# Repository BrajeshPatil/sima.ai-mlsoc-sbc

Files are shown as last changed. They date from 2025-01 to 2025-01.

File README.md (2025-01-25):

# sima.ai_mlsoc_sbc
The Single Board Computer designed using the SiMa.ai MLSoC is a part of a project that I did under ARTPARK. The SBC was designed to run computationally heavy software such as SLAM, VIO, and Autonomous Guidance Systems for UAV applications. The SiMa.ai MLSoC, a state-of-the-art ML-based SOC, was selected for this purpose.

This repository provides the design files for only the hardware part of the project. [Altium Designer](https://www.altium.com/altium-designer) has been used for designing the Single Board Computer.

# Hardware Architecture
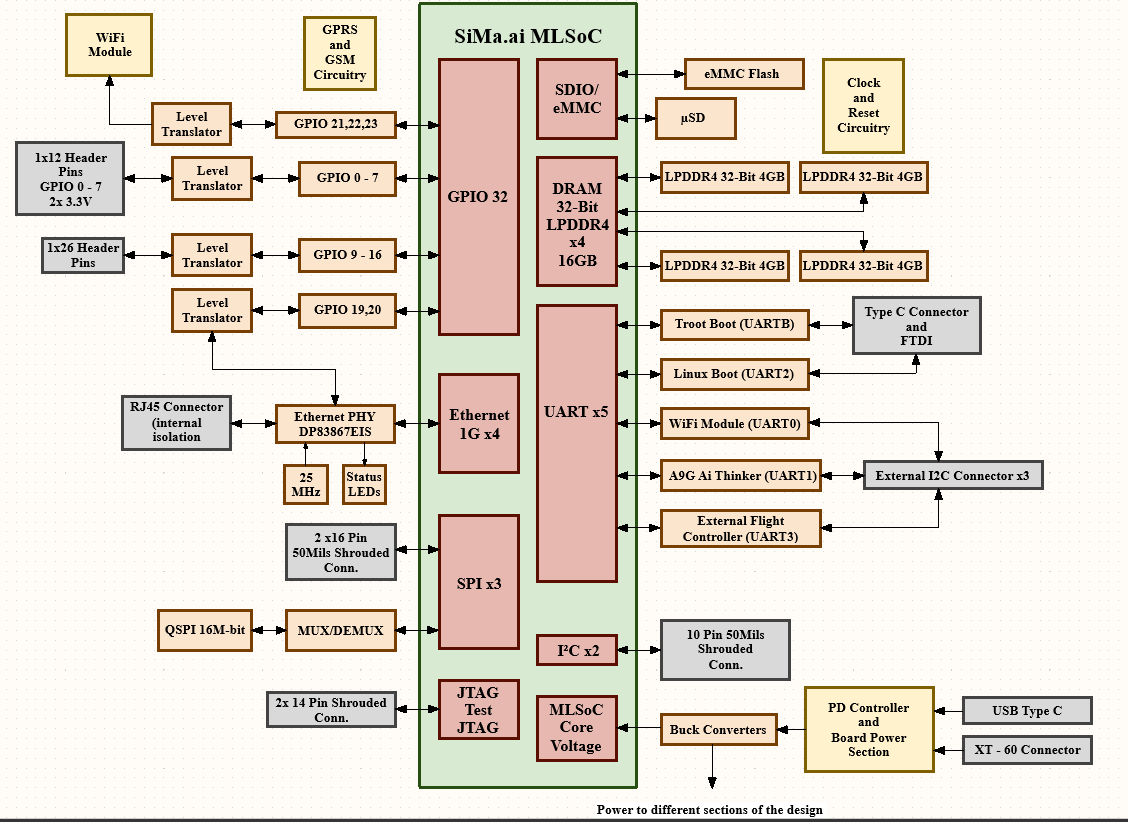
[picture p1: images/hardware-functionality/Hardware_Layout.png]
Hardware Layout


Features of the SBC:
1. SiMa.ai MLSoC provides 4 Ethernet Chipsets. Only 1 of these chipsets have been used in our SBC. The Ethernet PHY IC DP83867EIS has been used for implementing the physical layer for Communication. RJ45 Connectors with internal magnetic isolation have been used.
2. 5 UART Controllers have been used for working of the following sub-systems:
    - UART0 Controller has been used for functioning of the WiFi Module.
    - UART1 Controller has been used for functioning of A9G AI Thinker GSM and GPRS module.
    - Linux Boot functionality is provided by using UART2 and Troot Boot has been implemented using UARTB. These are also connected to FTDI chip so that the SBC can be booted using a Type C Cable.
    - UART3 currently doesn't have any functionality but has been made accessible. It can be used to communicate with an external UART device.
    - UART0, UART1 and UART3 have been connected to external I2C connectors.  
3. The SoC contains 32 GPIO pins. They are implemented as follows:
    - GPIO Pins 21, 22 and 23 have been used in the WiFi Module. As the WiFi Module works on 3.3V voltage level, a (1.8V to 3.3V) voltage translator has been used.
    - GPIO Pins 0 - 7 have been translated to 3.3V and have been provided externally.
    - GPIO Pins 9 - 16 have been translated to 5V and have been provided externally.
    - GPIO Pins 19, 20 have been used for functioning of the Ethernet PHY IC.
4.  DRAM (Dynamic Random-Access Memory) is fast, temporary storage that holds data while a computer runs, but it loses information when powered off. It stores data in capacitors that require periodic refreshing, using operations like activate, read/write, precharge, and refresh to manage access and integrity. 4x 32-bit LPDDR4 chipsets with P/N MT53E1G32D2FW-046 IT:B from Micron is mounted on the MLSoC Evaluation Board. The operating frequency of the LPDDR4 chip is 1866MHz.
5. The SBC can be powered through two ways, i) USB Type C and ii) XT-60 Connector.
    - The TPS548D22 IC is used to generate 0.85V Core Voltage.
    - SiC437DED used for generating 1.8V and 1.1V.
    - The PMIC Switching Regulator is used to generate 3.3V, 1.8V, 2.5V and 4.2V.
6. The SoC contains 3 SPI Buses.
    - 1 SPI Bus has been provided externally.
    - The other 2 SPI Buses have been used to implement a QSPI Flash Memory using a MUX and a DEMUX. 
7. The 2 I2C Buses have been provided on the SBC. These can be used for interfacing with sensors, storage devices, displays or any device working on I2C Protocol.
8. The eMMC interface includes a clock (CLK), command (CMD), and an 8-bit data bus (D0-D7), with separate power pins for core (VCC), I/O (VCCQ), and stabilization (VDDI). It also features DS for HS-400 mode, card detect (CRD DET N), and write protect (CRD WR PROT) functionality.
9. The MLSoCsupports SD3.0 controller interface for loading the boot files from an external SD card. A Micro-SD Push-Push connector with P/N 693071020811 is used for interfacing the external SD card with the MLSoC Evaluation Board.
10. JTAG Test functionality has been provided by providing access to them through a 2x14 Pin Shrouded Connector.
11. The GPS and GSM functionalities for tracking the vehicle's location and enabling SMS communication have been implemented using the A9G Ai-Thinker module. The clock and reset circuitry has also been employed. 

# File structure
The repository contains directories for all sub-sections of the hardware layout. In-depth explanation of all the sub-sections have been included in these directories.
```
.
│   LICENSE                        # This file contains the license information for the project.
│   README.md                      # This file provides an overview of the project.
├───Boot Modes and Status
│   │   README.md                  # Description of boot modes and status indicators.
│   └───Altium Designer Files      # Contains Altium Designer files related to boot modes and status.
├───DRAM Interface
│   │   README.md                  # Information about DRAM interface and configurations.
│   └───Altium Designer Files      # Contains Altium Designer files related to the DRAM interface.
├───Gigabit Ethernet
│   │   README.md                  # Details about Gigabit Ethernet setup and configurations.
│   └───Altium Designer Files      # Contains Altium Designer files for Gigabit Ethernet.
├───GPIO
│   │   README.md                  # General Purpose Input/Output (GPIO) configurations and usage.
│   └───Altium Designer Files      # Contains Altium Designer files for GPIO.
├───GSM and GPS Module
│   │   README.md                  # Documentation for GSM and GPS module integration.
│   └───Altium Designer Files      # Contains Altium Designer files for GSM and GPS module.
├───I2C Bus
│   │   README.md                  # Information about the I2C Bus interface and connections.
│   └───Altium Designer Files      # Contains Altium Designer files for the I2C Bus.
├───images
│   ├───hardware-design            # Images related to hardware design.
│   └───hardware-functionality     # Images showing hardware functionality.
├───Non Volatile Memory
│   │   README.md                  # Documentation on non-volatile memory usage and types.
│   └───Altium Designer Files      # Contains Altium Designer files for non-volatile memory.
├───Power Management
│   │   README.md                  # Details about power management strategies and configurations.
│   └───Altium Designer Files      # Contains Altium Designer files for power management.
├───SPI Bus
│   │   README.md                  # Information about SPI Bus interface and protocols.
│   └───Altium Designer Files      # Contains Altium Designer files for SPI Bus.
├───System Clocks
│   │   README.md                  # Documentation on system clocks and timing configurations.
│   └───Altium Designer Files      # Contains Altium Designer files for system clocks.
├───UART
│   │   README.md                  # Information about UART (Universal Asynchronous Receiver-Transmitter) interface.
│   └───Altium Designer Files      # Contains Altium Designer files for UART interface.
└───WiFi Module
    │   README.md                  # Documentation on WiFi module setup and configurations.
    └───Altium Designer Files      # Contains Altium Designer files for WiFi module.                   
```
# Contributors
- [Karteek Nayak](https://github.com/Karteek-N)
- [Brajesh Patil](https://github.com/BrajeshPatil)

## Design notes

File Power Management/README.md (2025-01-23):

# Power Management
### Power Input and Supply

The power section of this Single Board Computer (SBC) is designed to support multiple input options for versatility and efficiency. Below are the key features of the power input design:

#### Input Connectors
XT60 Connector: A robust input option suitable for high-current applications.
USB Type-C Connector: A modern and widely used connector for both data and power delivery.

#### USB PD Protocol
The power delivery system leverages the USB Power Delivery (USB PD) protocol to achieve higher power requirements, supporting up to 20V at 5A (100W). This enables the SBC to handle high-performance applications while maintaining efficient power utilization.

### Key Components
Communication Lines: The USB PD protocol relies on the CC1 and CC2 lines for communication. These lines establish a standardized negotiation process for voltage and current levels, ensuring compatibility and safety.

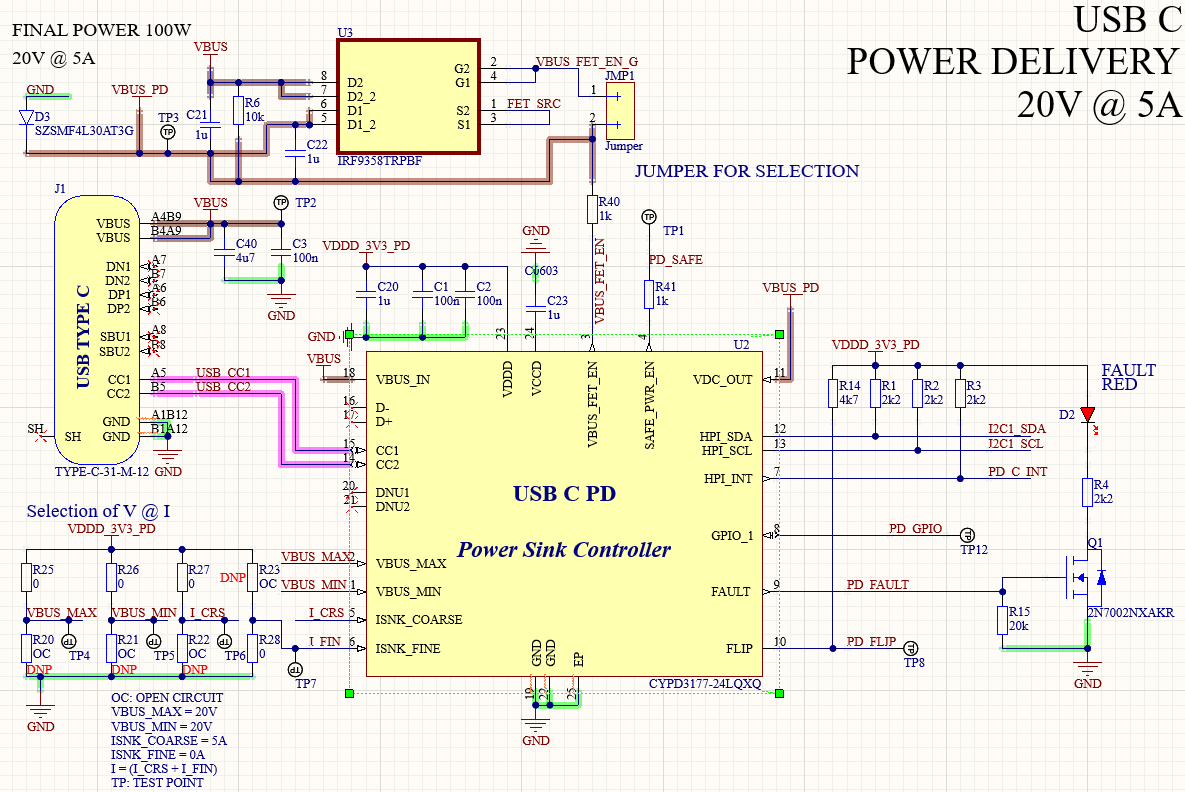
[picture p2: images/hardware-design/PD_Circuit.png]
Image description


Current Setting Lines: The CC1 and CC2 lines also play a crucial role in setting the appropriate current levels, adhering to the USB PD specifications.

PD Controller: The SBC uses the CYPD3177-24LQXQ by Infineon as the USB PD controller.

### Layout
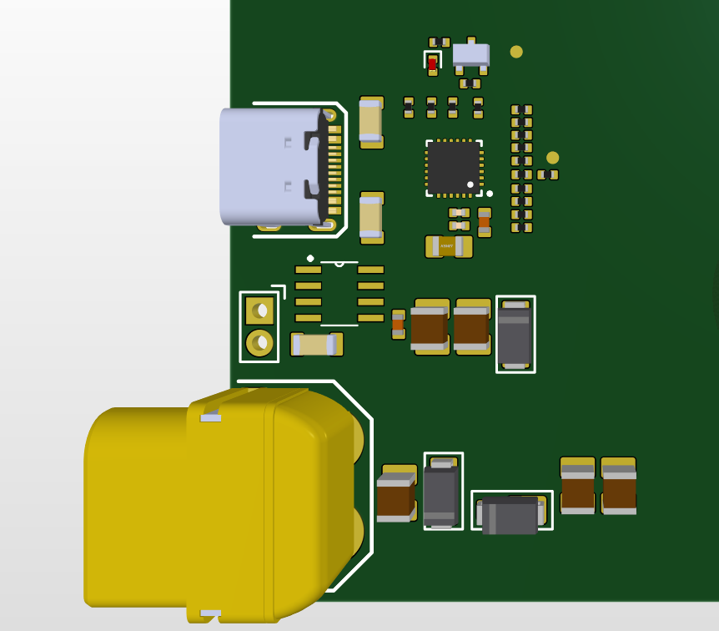
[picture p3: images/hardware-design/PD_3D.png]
Image description


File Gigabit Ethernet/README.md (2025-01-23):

# Gigabit Ethernet
This section explains the schematic design implementation of the Gigabit Ethernet using the DP83867 Ethernet PHY IC. This feature is added in our SBC so that the pilot can be able to communicate with other devices supporting Ethernet or get inbuilt access to the Internet and additional functionality can be added later as required.

### Hardware Architecture
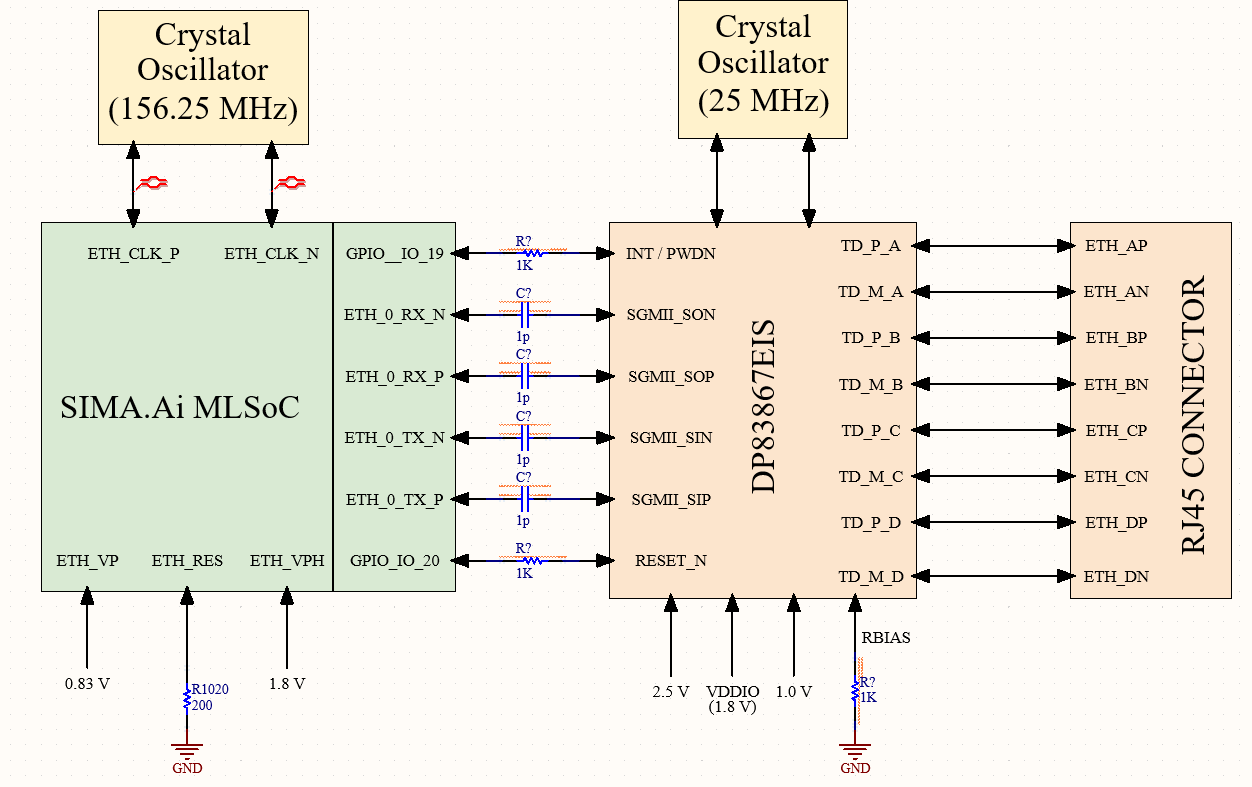
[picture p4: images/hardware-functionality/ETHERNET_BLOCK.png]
Hardware Layout


The MLSoC provides 4 chipsets of Ethernet but the SBC is provided with one Gigabit Ethernet chipset. The Ethernet MAC is interfaced with the RJ45 Magjack connector with the help of the Ethernet PHY DP83867EIS IC.
Magnetic isolation to prevent signal form back routing is also taken care of while designing. Appropriate Crystal values were used for the oscillators of the Ethernet MAC and the Ethernet PHY. 156.25 MHz Crystal was used for the internal working of the Ethernet MAC.

### Schematic
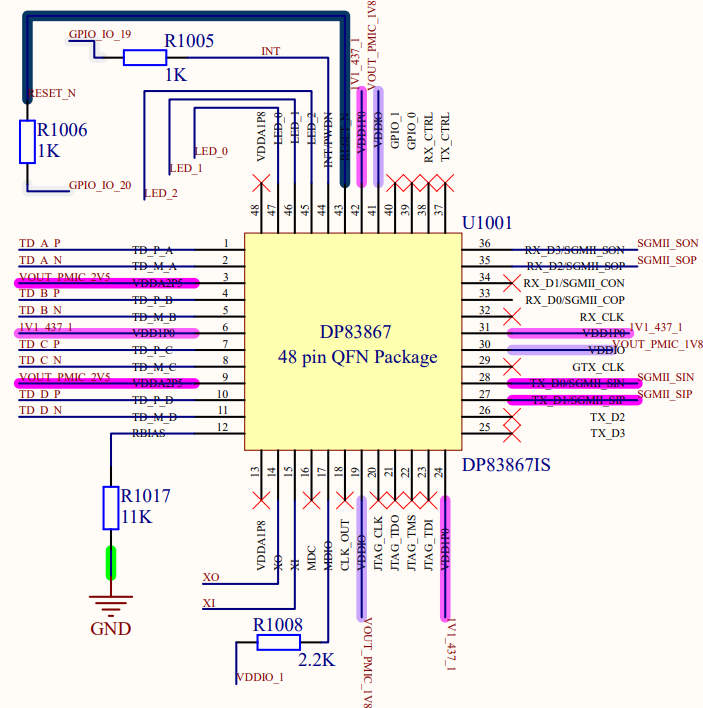
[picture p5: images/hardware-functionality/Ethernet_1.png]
Image description

We have used the 2 power supply mode of the IC. An 11kΩ bias resistor is used as per the datasheet. INT(44) and RESET N(43) are connected to MLSoC GPIOs for external user control.

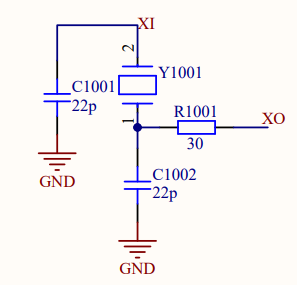
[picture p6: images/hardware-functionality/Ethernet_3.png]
Image description


The clock input is provided through a 25MHz crystal. The crystal load capacitance is calculated using ((CX1 x CX2) / (CX1 + CX2)) + Cstray. Resistance is 30 ohms and crystal load capacitance is 22pF. This crystal oscillator is connected to pins XO(14) and XI(15).

The Ethernet PHY is connected to MLSoC with the 4 pin mode. These 4 pins are SGMII_SON(36), SGMII_SOP(35), SGMII_SIN(28), SGMII_SIP(27). SGMII_SON and SGMII_SOP are used for the receiving signal and form a differential pair. They are connected to the ETH_0_RX_N and ETH_0_RX_P using a resistor divider network and 0.1µ F capacitors.

SGMII_SIN and SGMII_SIP form a differential pair and are used to transmit. Rhi = 4K and Rlo = 10K are used on pins 27,28,35,36.

The LED_0, LED_1 and LED_2 pins are used as strapping options to select particular modes.

### Power Sub-Section
Image description

It is possible to operate the DP83867 using two or three power supplies. Although the two supply configuration requires slightly more power, it requires less space as compared to its counterpart. So we have used the three power supply configuration.

VDDA1P8 pin is left unconnected. We have connected 1µF and 0.1µF decoupling capacitors as close as possible to component VDD pins and 0.1µF capacitor closest to the pin. In our SBC we have used VDDIO as 1.8 V. The power required for this IC is 495 mW.

### Boot Strapping
Image description

The DP83867 has multiple functional pins which provide strapping options which help the device work into specific modes. Values of these pins are sampled at power up or hard reset. Strap Configuration can be defined by two resistors Rhi and Rlo. Values of these resistors can be set in order to select one of the four modes. We have used SGMII ENABLE i.e. Mode 1 for LED_0.

### Ideal Resistor Values for Strapping Configurations
| Mode | Vmin (V) | Vtyp (V) | Vmax (V) | Ideal Rhi (kΩ) | Ideal Rlo (kΩ) |
|---|---|---|---|---|---|
| 1 | 0 | 0 | 0.098 * VDDIO | OPEN | OPEN |
| 2 | 0.140 * VDDIO | 0.165 * VDDIO | 0.191 * VDDIO | 10 | 2.49 |
| 3 | 0.225 * VDDIO | 0.255 * VDDIO | 0.284 * VDDIO | 5.76 | 2.49 |
| 4 | 0.694 * VDDIO | 0.783 * VDDIO | 0.888 * VDDIO | 2.49 | OPEN |

### Modes of Operation for LED_0
| Mode | Mirror Enable | SGMII Enable |
|---|---|---|
| 1 | 0 | 0 |
| 2 | 0 | 1 |
| 3 | 1 | 0 |
| 4 | 1 | 1 |

### Modes of Operation for LED_1
| Mode | ANEG_SEL | RGMII Clock Skew TX[2] |
|---|---|---|
| 1 | 0 | 0 |
| 2 | 0 | 1 |
| 3 | 1 | 0 |
| 4 | 1 | 1 |

### Modes of Operation for LED_2
| Mode | RGMII Clock Skew TX[1] | RGMII Clock Skew TX[0] |
|---|---|---|
| 1 | 0 | 0 |
| 2 | 0 | 1 |
| 3 | 1 | 0 |
| 4 | 1 | 1 |

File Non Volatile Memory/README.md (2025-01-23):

# Non Volatile Memory
The DRAM interface studied was a volatile memory, meaning that once the power is turned off, the data contents get erased off memory. However, if we want memory to be stored in an IC, we need to use Non-Volatile memory ICs like eMMC Flash, QSPI flash and µSD Card.

## eMMC Flash Memory
eMMC Flash Memory with P/N IS22TF16G-JCLA1 is being used in the DroneSense Board. ISSI eMMC products follow the JEDEC eMMC 5.1 standard. It is ideal for embedded storage solutions for industrial and automotive application, which require high performance across a wide range of operating temperatures.

### Hardware Architecture


- We have the main clock signal, which has different frequencies and can be set according to requirements. Similarly we have a command signal CMD.
- D0-D7 is the data bus.
- VCC is the supply voltage for controller and Flash memory power. VCCQ is the supply voltage for controller and Flash memory I/O power.
- The DS is used in HS-400 mode of the eMMC.
- The VDDI pin must be connected to a capacitor to ground to stabilize internal power.
- The eMMC CRD DET N pin is the Card detect pin, which is tied to 3.3V via resistor as it must be on always.
- eMMC write protect pin EMMC CRD WR PROT is used to configure eMMC as read only. By default, this pin should be pulled high (write protected, read only).

### Schematic


## SDIO Flash Memory
The MLSoC supports the SD3.0 controller interface, enabling the loading of boot files from an external SD card. SDIO (Secure Digital Input/Output) is used for high-speed data transfer, connecting the MLSoC to peripherals like storage devices, sensors, and other external components. This interface allows seamless communication between the MLSoC and SD cards, making it ideal for loading firmware, storing data, and expanding the system's memory capacity.

### Hardware Architecture


Features of the SDIO Interface Implementation:
- SD3.0 standard interface supports up to 104MBps bus speed.
- A Micro-SD Push-Push connector with P/N 693071020811 is used for interfacing the external SD card with the MLSoC Evaluation Board.
- SD3.0 standard requires voltage switching. After the initial negotiation with the SD card, the controller begins to switch the voltage from 3.3V to 1.8V. So a level translator is a must to switch the voltage level from 3.3V to 1.8V if the card is detected as SD3.0.
- An SD3.0 compliant level translator with P/N NVT4857UKAZ from NXP semi-conductors takes care the aforementioned switching requirement.
- This level translator IC has integrated EMI filter and ESD protection circuitry on the output side.
- For input ESD and EMI Filtering, we have used a Filtering IC with P/N EMIF06-MSD02N16.
- Both pull-up and pull-down options are provided for write protect signal SD WP, and by default, this pin is pulled high.

### Schematic


## QSPI Flash Memory
### Hardware Architecture


The following things can be said about QSPI Flash used on the Single Board Computer:
- Three Octal SPI controllers are present in the MLSoC chipset, namely SPIB, SPI0 and SPI1.
- The SPIB controller from the MLSoC is used to connect the SPI flash, where the initial boot loader is present and the MLSoC boots after power on by reading this flash.
- 16Mbit Quad SPI flash IC with P/N W25Q16JWSNIQ TR is used as boot ROM. This IC is an 8-bit SPI with maximum clock rate of 133MHz.
- An additional 10-pin 100 Mils header is included for programming the SPI flash externally using an SPI programmer device. The same is used for analyzing the SPI signals as well.
- Once the MLSoC goes out of reset, it drives the SPB signals. Hence signals from the MLSoC and external programmer are connected to SPI via 6 bit 2:1 multiplexer IC with P/N TS3A27518ERTWR.
- Multiplexing functionality is controlled via the IN1 and IN2 pins, connected to a DIP switch P/N 219-3LPST. Alternatively, GPIOs can be used for control.

### Schematic


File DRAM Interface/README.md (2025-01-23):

# DRAM Interface
4x 32-bit LPDDR4 chipsets with P/N MT53E1G32D2FW-046 IT:B from Micron are mounted on the MLSoC Evaluation Board. These DRAM modules provide high-speed, low-power memory, essential for storing and accessing large datasets efficiently. The LPDDR4 memory is crucial for applications such as data buffering, real-time processing, and running memory-intensive tasks, ensuring optimal performance for embedded systems.

### Hardware Architecture


Features of the LPDDR4 Implementation in the MLSoC:
- Each LPDDR4 chipset is of 4GB density. Each chip has operating frequency 1866MHz clock rate, which is same as that of MLSoC memory controller operating frequency.
- All signals are of LVSTL IO standard.
- Power requirement of each LPDDR4 IC is as follows:
  - VDD1 = 1.8V
  - VDD2 = 1.1V
  - VDDQ = 1.1V
- LPDDR4 chipset requires power sequencing:
  - VDD1 must ramp at the same time or earlier than VDD2.
  - VDD2 must ramp at the same time or earlier than VDDQ.
  - VDD1must be greater than VDD2 and VDD2 must be greater than (VDDQ - 200mV).
- 4 individual DRAM controllers are present in the MLSoC, hence for command/address, control, and data signals, point to point routing topology is used between MLSoC and LPDDR4 chipset.
- The ZQ calibration pins are connected to VDDQ through 240 ±-1% resistor.
- LPDDR4 chipset command or address ODT control signals, ODT_CA_A,ODT_CA_B are pulled to VDD2 for enabling on-die termination.

### Implementation of LPDDR4
Following are the reasons for selecting the aforementioned LPDDR4 device:
- Selected LPDDR4 supports 32 Bit IO channels.
- Industrial grade LPDDR4 parts are readily available.
- Available at a cost effective price.
- LPDDR4 IC from Micron has been tested successfully.

### Schematic
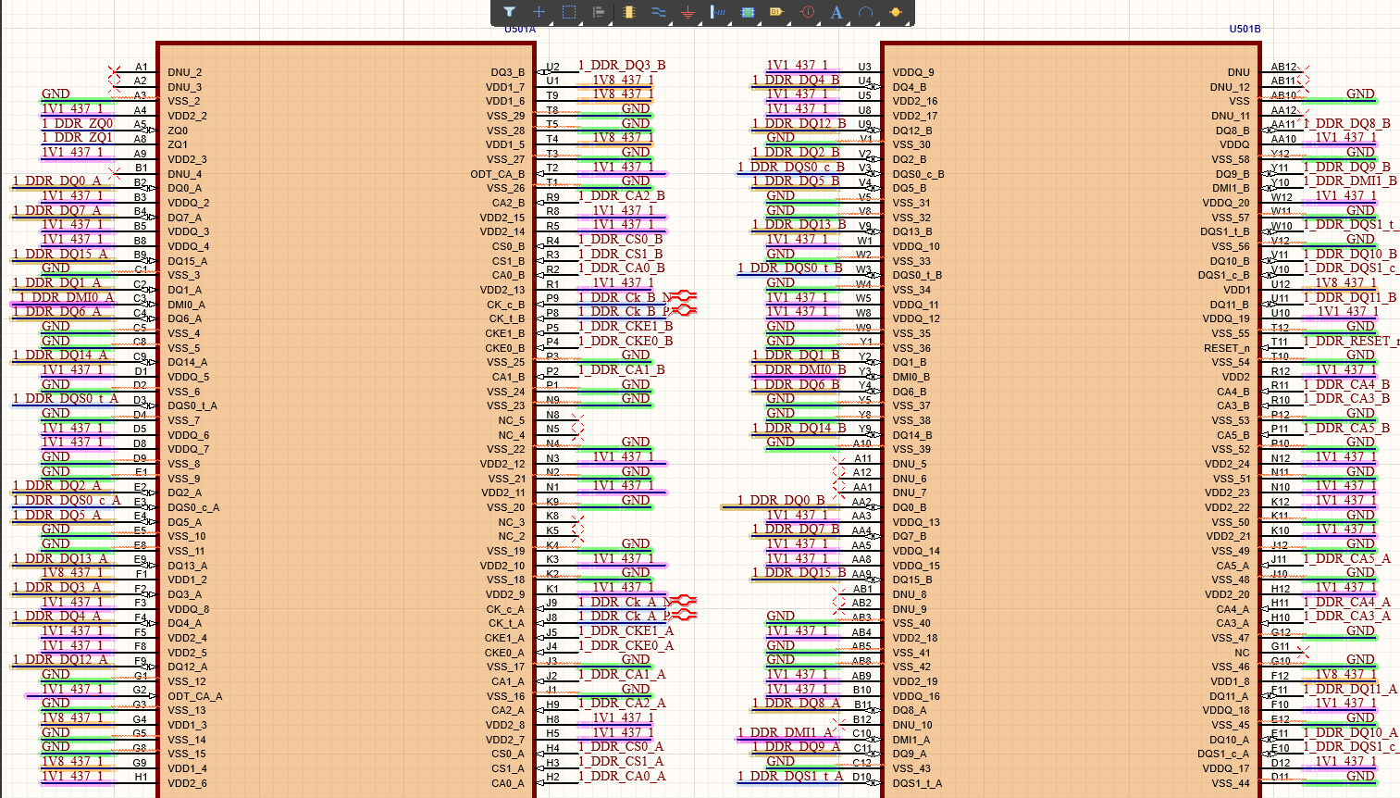
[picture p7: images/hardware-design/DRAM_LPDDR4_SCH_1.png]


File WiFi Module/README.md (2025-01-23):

# WiFi Module
WiFi Module has been integrated in our SBC in order to enable wireless communication with the controller. The Wifi module is designed using the ESP8266ex IC and a PCB antenna is made on the board.

### Hardware Architecture
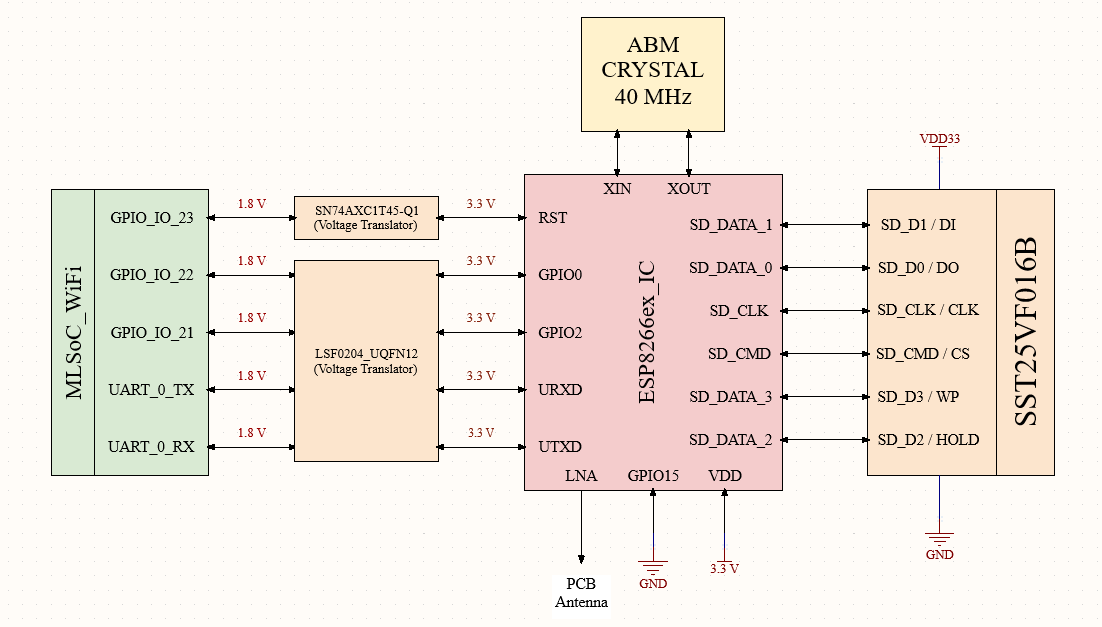
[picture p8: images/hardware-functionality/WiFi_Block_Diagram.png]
Hardware Architecture

We have used the ESP8266ex IC for designing the WiFi module for the SBC as it has open source software and hardware, also it is easily available and programmable. The WiFi module uses UART_0 chipset for communication. A PCB antenna supporting 2.4GHz communication and having 50Ohm impedance is used for increasing signal strength. This antenna connected to the output of the Low Noise Amplifier. 

A 40 MHz ABM crystal is used for time synchronization. LSF0204- Quad Bit and SN74 Single Bit Voltage Translators are used to translate voltages from 1.8V to 3.3 V. The 8 pin SST25VF016B 16Mbit Serial Flash is used to store Firmware. The GPIO pins from MLSoC are connected to the RST, GPIO2 and GPIO 0 of the WiFi module for external control of modes. The ESP8266ex IC works on 3.3 V level.

### Schematic
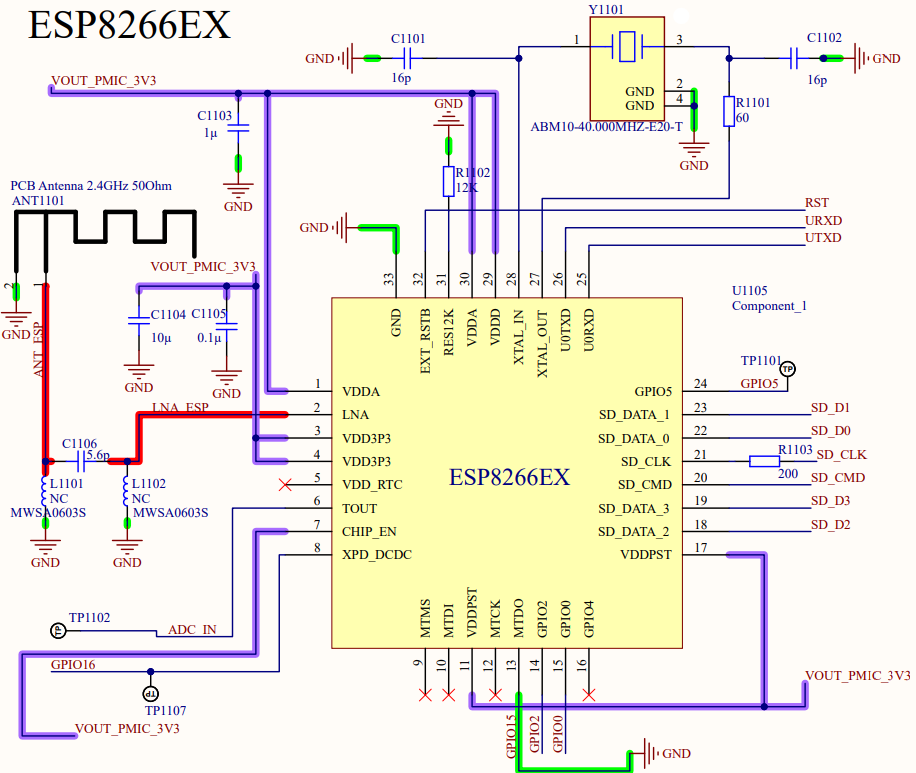
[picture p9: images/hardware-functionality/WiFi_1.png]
Image description


The ESP8266ex IC works on 3.3V logic. The power pins VDDD(29), VDDA(1, 30), VDDPST(11, 17), and VDD3P3(3 , 4) are supplied with 3.3V generated in the power section. The Chip_EN pin is also connected to 3.3V.

A PCB antenna which is created by forming paths on the top layer of the board is used to increase signal strength of the Low Noise Amplifier Output. The two inductors and one capacitor are used to retain as much power as possible which can be transmitted by the antenna.

The pins ADC_IN(6), GPIO16(8), GPIO5(24) are created as test points which can be used to inject signals or monitor the circuitry. As per the datasheet a bias resistor of 12K is used on RES12K (31) pin. UART_0 of the SiMa.ai MLSoC is used for communication with the ESP8266ex. Also the three GPIO pins 21, 22 and 23 are used.

### ESP FLASH
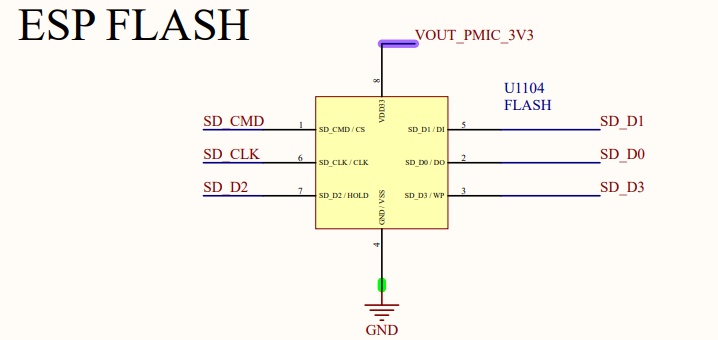
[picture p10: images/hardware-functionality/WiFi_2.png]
Image description


Pins 18-23 connect to the SST25VF016B SPI Flash for firmware storage, with SD CLK using a 200Ω series resistor. The SPI Flash operates on 3.3V logic. The ESP8266EX RST pin is connected to MLSoC GPIO 23, allowing user-controlled resets.

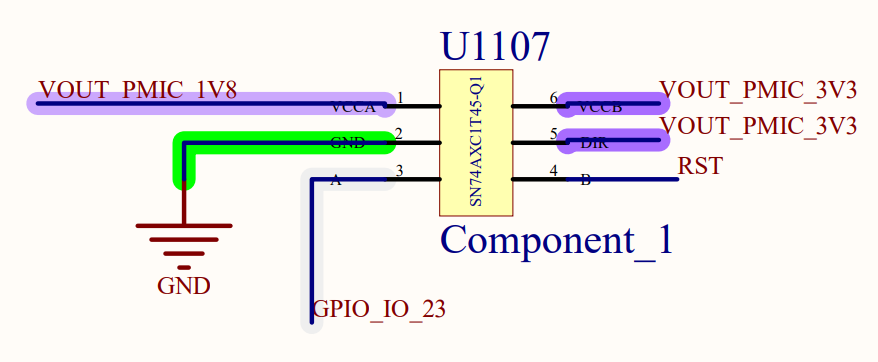
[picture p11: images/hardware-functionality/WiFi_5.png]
Image description


The SN74XC1T45-Q1 voltage translator converts MLSoC 1.8V logic to WiFi module 3.3V logic. DIR is set to logic 1 for signal flow to the ESP8266EX RST pin.

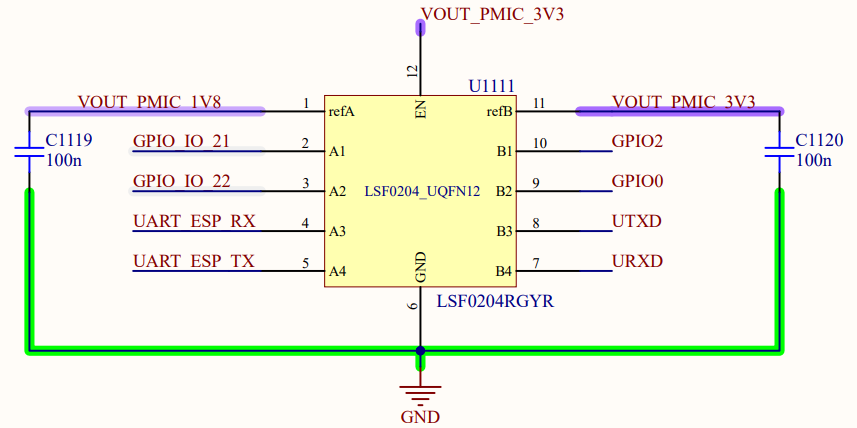
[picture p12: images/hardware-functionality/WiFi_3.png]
Image description

 
Similar to the RST pin, the GPIO2(14), GPIO0(15) are also connected to the GPIO 21 and GPIO 22 pins of the MLSoC. The Level translator used in this case is LSF0204 Quad Bit level translator. The IC Quad bit so it can translate four signal lines at a time. The other two inputs of this level translator are used to convert 1.8 V UART signals (UART_0_RX and UART_0_TX) from the MLSoC to 3.3V UART signals UTXD (25) and URXD (26) of the ESP8266ex.

### Mode Selection
The WiFi module can work in two modes. One of the modes is UART mode in which the WiFi module can communicate with other users. The other mode is Flash Boot mode which can be used to install or update the firmware in the external SPI flash. These modes can be selected by changing logic values on the GPIO15, GPIO2 and GPIO0 of the Circuit.

The following is dependency of the modes on these GPIO pins:
- If GPIO15 is LOW, GPIO0 is LOW and GPIO2 is HIGH then UART Mode is
 selected.
- If GPIO15 is LOW, GPIO0 is HIGH and GPIO2 is also HIGH then SPI Flash Boot
 Mode is selected.

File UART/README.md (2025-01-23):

### UART: Hardware Architecture


The information related to UART is given below:

- The FT2232HL-REELIC is used as a USB-to-UART transceiver for Linux Boot (UART2) and Troot Boot (UARTB).  The VBUS voltage from the USB Type-C connector (P/N TYPE-C-31-M-12) is directly connected to the RESET pin of the FTDI.
- VCCIO for FT2232HL transceiver IC is provided with 1.8V on-board power supply to match the MLSoC IO voltage characteristics.
- Pair of LEDs are used for both Linux Boot ans Troot Boot to indicate the transmit state and receive state of the signal through UART.
- Alevel translator with P/N TXS0102DCUT is used to convert the MLSoC UART signals to 3.3V I/O level.
- The rest of three general purpose UARTs are connected to external header pins with Pitch as 100Mils and 4 POS Header pin. They have been level translated from 1.8V to 3.3V using P/N TXS0102DCUT.
- UART0 interfaces with the ESP8266ex WiFi module and can also be accessed externally via a header using the TMUX121NKGR multiplexer, controlled by a 219-3LPST DIP switch. Similarly, UART2 and UART3 connect to external headers via the same multiplexer. UART1 connects to the A9G module (TX-RX) through a 1.8V to 2.8V level translator.
- All UART pins on the connector have been ESD protected using Protection diodes with P/N ESDR0524SMUTAG.

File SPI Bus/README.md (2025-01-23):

# SPI Bus
Serial peripheral interface (SPI) allows synchronous serial communication (full duplex or half duplex) with continuous streaming of data communicated between the controller and one or more peripheral devices. The dual embedded SPI controllers allow the MLSoC to communicate with external sensors, ADCs, flash memory, and other low data-rate peripherals. We have more two SPI controllers present in the MLSoC. These are SPI0 and SPI1. The following are the features of these controllers:
  - 8-bit operation
  - Four Slave Selects
  - Dual Master/Slave operation
  - 25 MHz SDR operation

### Hardware Architecture
Image description

- SPI0 and SPI1 are the two SPI interfaces present in the MLSoC.
- Since we are already using one Quad SPI with QSPI Flash Memory, what we need to do is connect the SPI0 and SPI1 to connectors. Thus, the SPI0 and SPI1 are connected to an external 20 POS header connector with P/N 70246-2001.
- To connect to the header, the voltage must first be translated from 1.8V to 3.3V. An 8-bit level translator, TXS0108EPWR, is used for this purpose.
- Since we have more number of SPI pins, we’ll be connecting the other pins to 4bit Level Translators with P/N TXS0104EPWR.

### Schematic


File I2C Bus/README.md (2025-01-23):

# I2C Bus
This section discusses about the implementation of two I2C Buses in the design. I2C is an important communication protocol which can be used to communicate with sensors or other external devices through its two buses, a Clock Pin and a Data Pin.

### Hardware Architecture

- The MLSoC provides two I2C buses: I2C0 and I2C1, each with SDA (data) and SCK (clock) pins.
- MLSoC I2C operates on 1.8V logic, while most sensors use 3.3V logic.
- A voltage translator TXS0104EPWR (Quad Bit Voltage Translator) is used to convert 1.8V to 3.3V.
- Translation mapping:
    - 1.8V buses at A1, A2, A3, A4 → 3.3V buses at B1, B2, B3, B4.
- 4.7k ohm pull-up resistors are used on both sides of the voltage translator.
- The 3.3V I2C buses are connected to a 15-91-6082 C-Grid Connector, which also operates on 3.3V logic.
- Users can access the 3.3V I2C buses via the C-Grid Connector.

### Schematic


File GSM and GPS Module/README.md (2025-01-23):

# GSM and GPS Module
In order to track location of the drone and to add one more communication method through SMS, the GPS and GSM Module has been developed. These functionalities are designed using the A9G Ai-Thinker Module.

### Hardware Architecture

The block diagram above explains the GSM and GPS Module which we have designed.The A9G Ai Thinker IC is used for this purpose. The circuit has an in-built Micro-Sim, Microphone and antennas for GPRS and GPS. The Micro-Sim used is 78646-3001. 

VSIM, SIM_RST, SIM_CLK and SIM_DIO are connected to the equivalent pins on the A9G Ai Thinker. The I2C and SPK buses are provided to the user through 01x08 Connector. The Microphone Signal has two differential pins which are interfaced using the ICS_40720 IC. The UART1 chipset from the MLSoC is used provided to the A9G Ai Thinker after voltage translation from 1.8V to 4V. UART1_CTS and UART1_RTS pins are provided as test points for the user.

### Schematic


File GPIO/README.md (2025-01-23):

# GPIO
The MLSoC supports 32 GPIO for various I/O operations. An ESD protection is added for all the GPIO signals. Following is the list of GPIOs and there use cases:
  - GPIO[7:0] are connected to an external connector with P/N M20-7810645R. The I/O logic is 1.8V, so these GPIOs pass through a level translator, P/N TXS0108EPWR. The connector has a max current rating of 3A. These GPIO pins can also be used for interrupting the APU. GPIO[8] enables the level translator, P/N NVT4857UKAZ, used in the SDIO interface.
  - GPIO[16:9], GPIO[18] and GPIO[28:24] are connected to a 26-pin external connector with P/N 2-1761603-9. No level translator is used with these GPIO pins.
  - GPIO[19] and GPIO[20] are used in interfacing with the Ethernet Transceiver. GPIO[23:21] are used for interfacing with the ESP8266ex WiFi Module.
  - GPIO[29] is connected with a LED for testing purposes.
  - GPIO[30] and GPIO[31] are used to software switch the multiplexer with P/N TS3A27518ERTWR used in QSPI flash.

### Schematic



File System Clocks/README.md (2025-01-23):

# System Clocks
Clocks are used in order to provide time synchronization to the circuit. The table given below contains all the Reference Clocks used:
### Table of Oscillator Frequencies and Specifications

| Item No. | Oscillator Frequency | Clock Source | Frequency Stability | Device | Interface |
|---|---|---|---|---|---|
| 1 | 33MHz | Crystal | 10ppm | MLSoC  | MLSoC Reference Clock |
| 2 | 32.768kHz | Crystal | 20ppm | MLSoC  | RTC Reference Clock |
| 3 | 156.25MHz | Crystal | 50ppm | MLSoC  | Ethernet MAC Reference Clock |
| 4 | 25MHz | Crystal | 25ppm | Ethernet Physical IC | Reference Clock for Ethernet Physical IC |

### Schematic


The Reference clock used for the Ethernet Physical IC is mention in the Gigabit Ethernet Section.

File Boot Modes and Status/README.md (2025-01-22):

# Boot Modes and Status
This is a part of the MLSoC which contains the pins for the Boot modes and the System pins. The System pins can be used in order monitor the status of the SBC. So the four System pins have been connected to test points which can be easily accessed by the user to check system conditions.

Image description

There are four Boot Mode Pins present in the MLSoC. These pins along with the QSPI interface can be used to select the Boot Mode of the SBC. In order to provide control over selection of boot modes to the user we have connected these pins to DIP switches which can be used to pull-up or pull-down the pins.

Image description

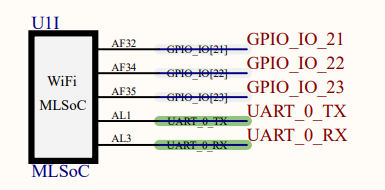
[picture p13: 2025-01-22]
images/hardware-functionality/WiFi_4.png

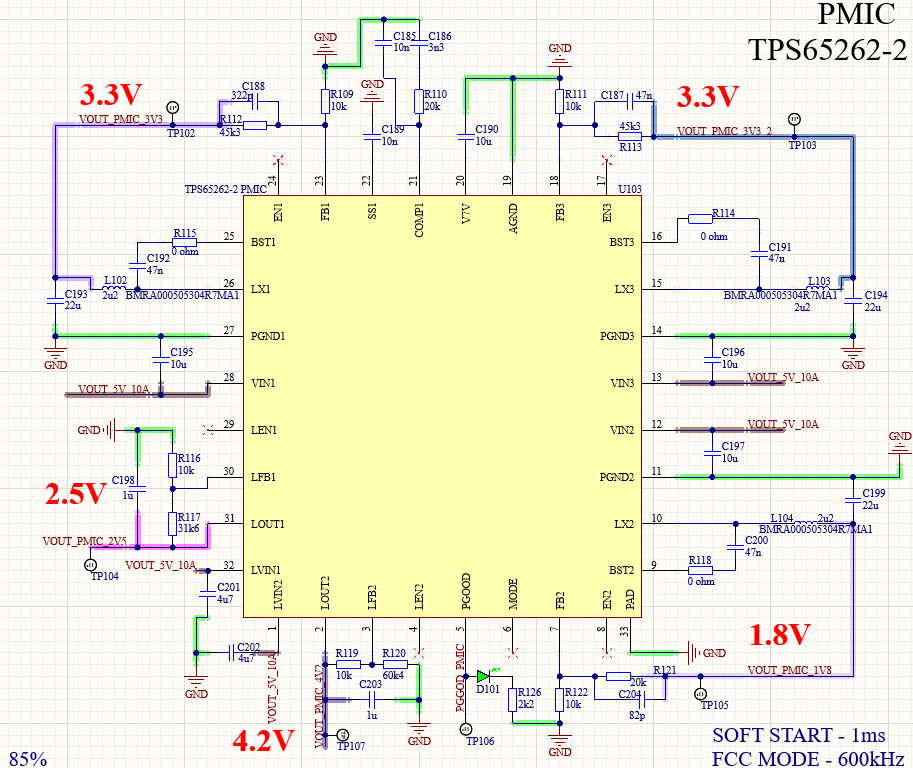
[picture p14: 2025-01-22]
images/hardware-design/PMIC_SCH.png

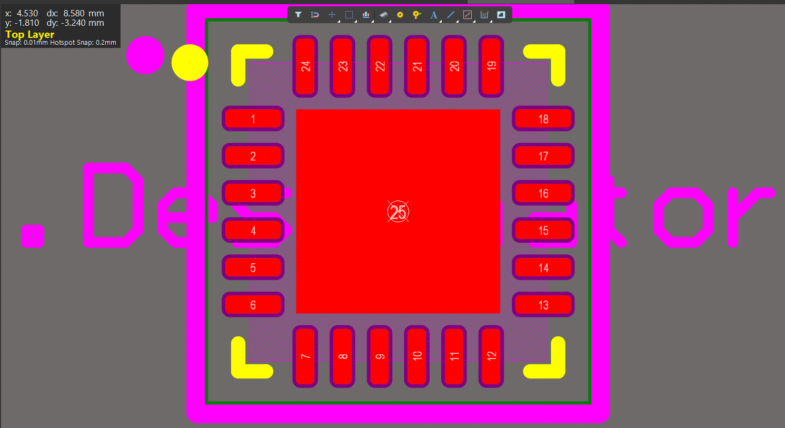
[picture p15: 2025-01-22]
images/hardware-design/PD_Controller_Footprint.png

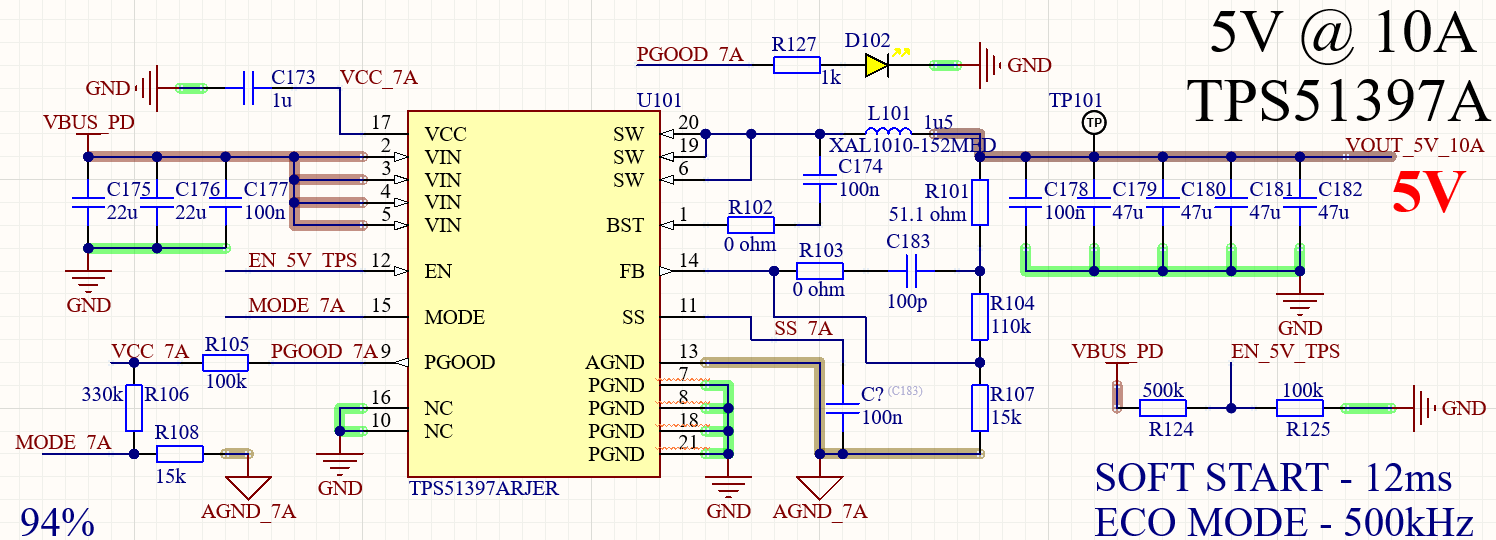
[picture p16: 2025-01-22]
images/hardware-design/TPS_5V_PERI_SCH.png

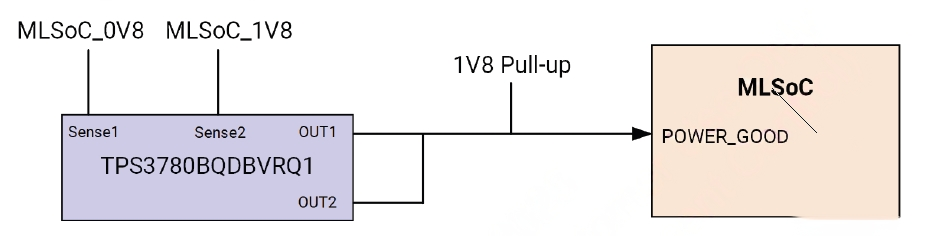
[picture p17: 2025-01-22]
images/hardware-design/POWERGOOD_SUPER_BLOCK.png

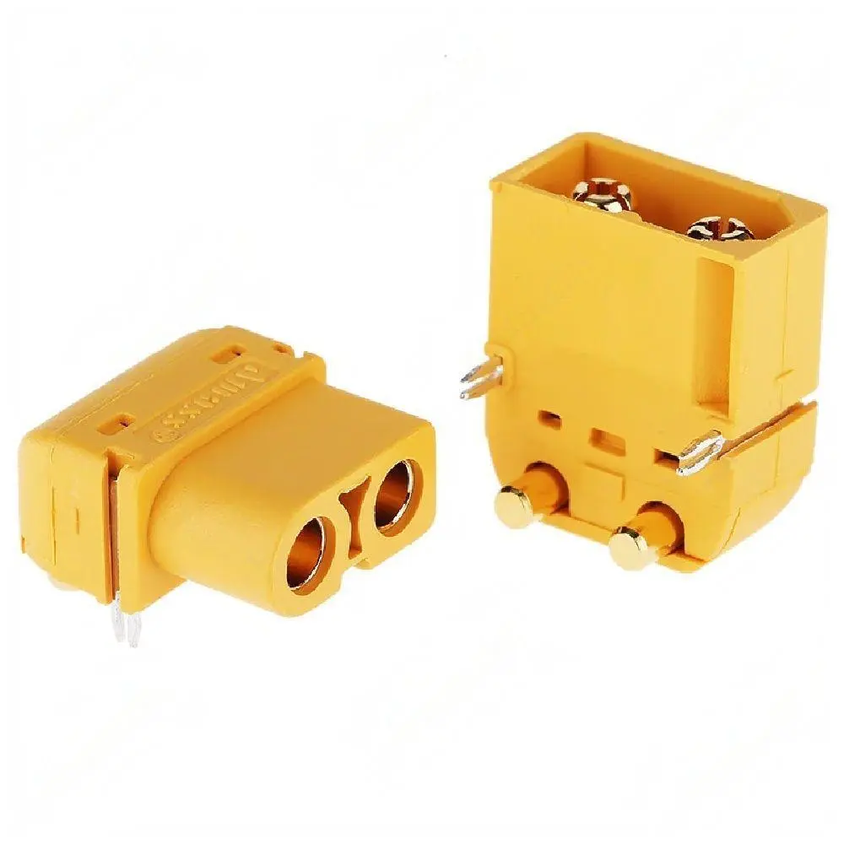
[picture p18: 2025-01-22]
images/hardware-design/XT60_Conn.webp
